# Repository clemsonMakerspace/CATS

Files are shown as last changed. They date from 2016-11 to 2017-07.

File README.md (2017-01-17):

CATS
====

The Clemson (Machinery) Access Tracking System, or CATS, is a [Creative Inquiry](http://www.clemson.edu/academics/programs/creative-inquiry/) project at Clemson University.

The goal of the project is to come up with an open-source system that can track and control machine access
at the Makerspaces on the campus.  As we work on the design process, we document our progress in our blog,
which you can find [here](http://ci.clemson.edu/blogs/cats/).

----

### Dependencies

This is a Python 3.x program dependent on the following libraries:
   1. `sys` - Python sys Libary
   2. `time` - Python time library
   3. `pymysql` - Python MySQL client
   4. `datetime` - Python datetime library
   5. `os` - Python os library (Python operating system interface)
   6. `RPi.GPIO` - package for controlling Rasberry Pi GPIO
   7. `string` - Python string library
   8. `InputDevice from evdev` - function from evdev package for Linux inputs
   9. `select from select` - Python select function from select library
   
These dependencies can be installed with the 'setup.sh' shell script found within.

### Configuration

TODO

### Usage

TODO

### License

The Clemson (Machinery) Access Tracking System is free software: you can 
redistribute it and/or modify it under the terms of the GNU Lesser General 
Public License as published by the Free Software Foundation, either version 
3 of the License, or (at your option) any later version.

The Clemson (Machinery) Access Tracking System is distributed in the hope 
that it will be useful, but WITHOUT ANY WARRANTY; without even the implied 
warranty of MERCHANTABILITY or FITNESS FOR A PARTICULAR PURPOSE.  See the
GNU Lesser General Public License for more details.

You should have received a copy of the GNU Lesser General Public License
along with this program.  If not, see <http://www.gnu.org/licenses/>

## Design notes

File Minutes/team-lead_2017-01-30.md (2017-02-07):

Team Lead Meeting Minutes
====

2017-01-30

10:10 AM - Start

####Attendees:
* Giandre Acosta
* Brice Grooms
* Owen Phillips
		
###New Meeting Formats
* Meeting minutes will be kept at all future team meetings held by Giandre, Brice, and/or Owen
* Meeting agendas will be distributed for all future team meetings held by Giandre, Brice, and/or Owen

###Team Meeting Summaries
#####Hardware
* Housing is currently discussing options
* PCB will hopefully be ready to order Friday
	* Owen will check with A. Hoover regarding purchasing requirements
	* Design will feature parallel routes for SMD and TH components
	* Will feature headers instead of raw wiring
* HID Omnikey 5321 has been recommended, will be ordered by Owen
	* Brice will submit a link for the 5321
	* Hardware team has promised to take ownership of software change for 5321

#####Software
* Software is working to introduce new devs to code base
* Brad is making headway on web admin panel - should be ready for additional help by Wednesday
		
###Goals for This Week
#####Software
* Giandre and Owen will work to setup test env with mocks for libraries like RPi.GPIO
* Team members will take ownership of certain functions and write tests
* Refactor at a later date
* Eduroam will be tested on a Raspberry Pi this week

#####Hardware
* Hardware will create BOM prior to purchasing PCBs
* Waterproofing has been de-prioritized in order to focus on immediate needs

#####Misc
* Hardware and Software leaders will debate use of Neopixel vs Traditional LEDs and select one by Friday

###Management Discussion
* Teams will utilize Waffle to track action items
* Teams should have retrospectives / standups to discuss work completed throughout the week
* Meetings should serve a purpose, anyone not necessary for the discussion should be dismissed

11:00 AM - Adjourn

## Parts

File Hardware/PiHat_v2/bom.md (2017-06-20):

Name            | Supplier | Part Number       | Quantity | Unit Cost | Link
----------------|----------|-------------------|----------|-----------|----------------------------------------------------------------------------------------------------------------
Neopixel        | Adafruit | 1655              | 5        | $0.45     | [Link](https://www.adafruit.com/product/1655)
Standoffs       | Adafruit | 2336              | 1        | $0.75     | [Link](https://www.adafruit.com/product/2336)
RPi GPIO Header | Adafruit | 2222              | 1        | $1.50     | [Link](https://www.adafruit.com/product/2222)
ATMEGA328P      | Digikey  | ATMEGA328P-AU-ND  | 1        | $2.07     | [Link](https://www.digikey.com/product-detail/en/microchip-technology/ATMEGA328P-AU/ATMEGA328P-AU-ND/1832260)
EEPROM          | Digikey  | CAT24C32WI-GOS-ND | 1        | $0.26     | [Link](https://www.digikey.com/products/en?mpart=CAT24C32WI-G&v=488)
Temp Sensor     | Digikey  | 568-4688-1-ND     | 1        | $0.74     | [Link](https://www.digikey.com/product-detail/en/nxp-usa-inc/LM75BD,118/568-4688-1-ND/1993025)
Piezo           | Digikey  | 102-1266-1-ND     | 1        | $2.08     | [Link](https://www.digikey.com/product-detail/en/cui-inc/CT-1205H-SMT-TR/102-1266-1-ND/610974)
Ethernet Jack   | Digikey  | RJHSE-5080-ND     | 1        | $0.91     | [Link](https://www.digikey.com/product-detail/en/amphenol-commercial-products/RJHSE-5080/RJHSE-5080-ND/1242687)
ISP Header      | Digikey  | 952-2120-ND       | 1        | $0.27     | [Link](https://www.digikey.com/product-detail/en/harwin-inc/M20-9980345/952-2120-ND/3728084)
1x2 Header      | Digikey  | 952-2261-ND       | 6        | $0.15     | [Link](https://www.digikey.com/product-detail/en/harwin-inc/M20-9990245/952-2261-ND/3728225)
Shunt Jumper    | Digikey  | 3M9580-ND         | 1        | $0.10     | [Link](http://www.digikey.com/scripts/DkSearch/dksus.dll?Detail&itemSeq=231061205&uq=636334990418973231)
16MHz Crystal   | Digikey  | 535-10226-1-ND    | 1        | $0.25     | [Link](https://www.digikey.com/products/en?keywords=535-10226-1-ND)
20pF Cap        | Digikey  | 311-1424-1-ND     | 2        | $0.10     | [Link](https://www.digikey.com/product-detail/en/yageo/CC0603JRNPO9BN200/311-1424-1-ND/2833730)
0.1uF Cap       | Digikey  | 311-1361-1-ND     | 1        | $0.10     | [Link](https://www.digikey.com/product-detail/en/yageo/CC0805ZRY5V9BB104/311-1361-1-ND/2103145)
1000uF Cap      | Digikey  | 493-2160-1-ND     | 1        | $0.48     | [Link](https://www.digikey.com/product-detail/en/nichicon/UWT0J102MNL1GS/493-2160-1-ND/590135)
1K Resistors    | Digikey  | 311-1.0KARCT-ND   | 4        | $0.10     | [Link](https://www.digikey.com/product-detail/en/yageo/RC0805JR-071KL/311-1.0KARCT-ND/731165)
3.9K Resistor   | Digikey  | 311-3.9KARCT-ND   | 2        | $0.10     | [Link](https://www.digikey.com/product-detail/en/yageo/RC0805JR-073K9L/311-3.9KARCT-ND/731252)
10K Resistor    | Digikey  | 311-10KARCT-ND    | 1        | $0.10     | [Link](https://www.digikey.com/product-detail/en/yageo/RC0805JR-0710KL/311-10KARCT-ND/731188)

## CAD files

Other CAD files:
Hardware/CATS Enclosure/V0.2 Drawing.SLDDRW

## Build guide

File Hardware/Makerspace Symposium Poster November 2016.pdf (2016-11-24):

RESEARCH POSTER PRESENTATION DESIGN © 2015
www.PosterPresentations.com

Makerspace equipment often has inherent risks to its users. These risks can be reduced by training operators. An additional approach to reduce these risks is to install technology that restricts access to untrained users.

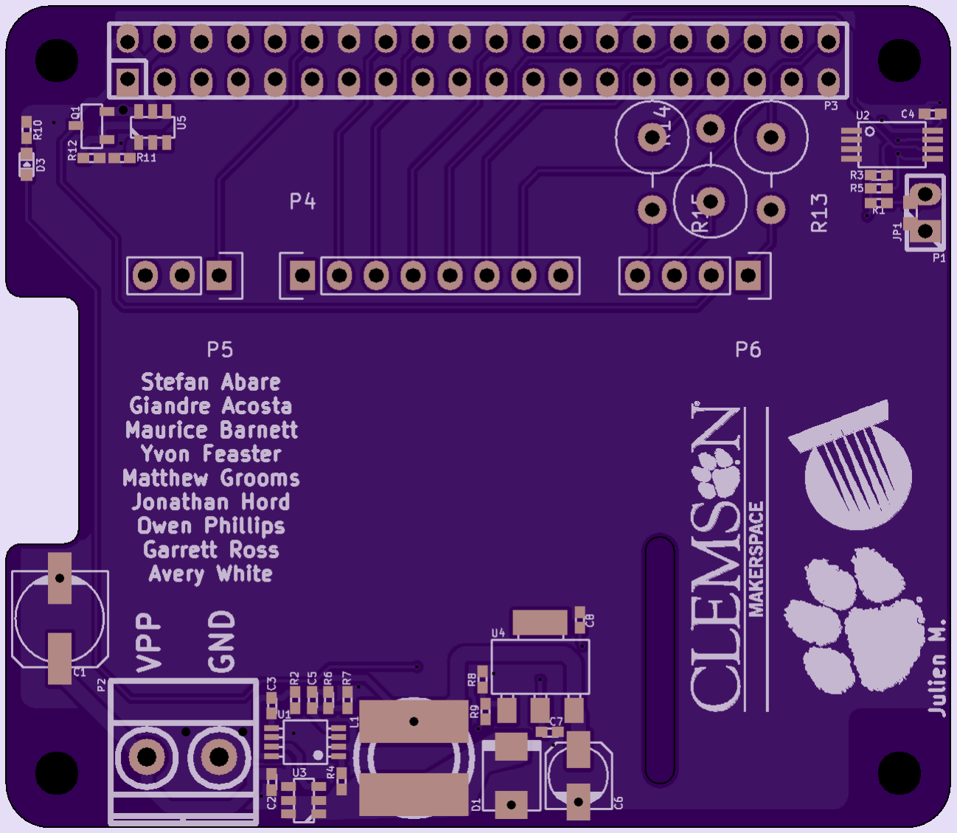
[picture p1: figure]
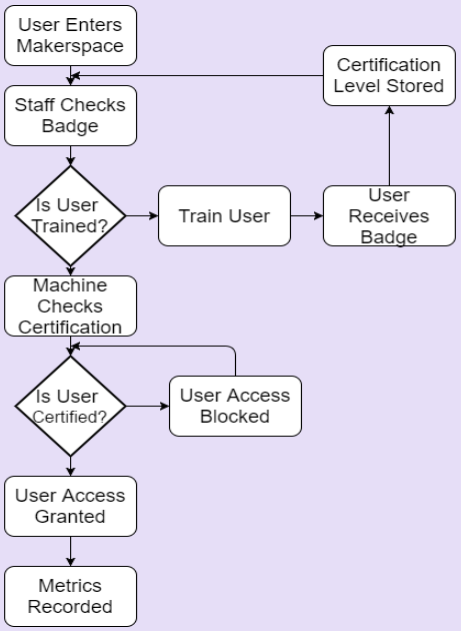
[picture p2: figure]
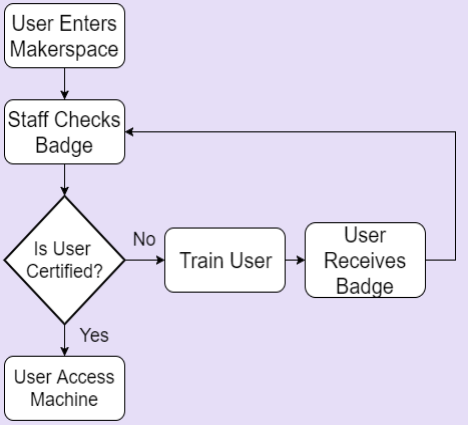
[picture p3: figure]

The Clemson [Machinery] Access Tracking System (CATS) is in development to create a more efficient way to operate a student space by automating the authentication process for a machine, so it will only power on for persons with permissions. Using CATS, facilities will be able to secure their machines by requiring students to provide credentials using their campus ID cards, and RFID card readers on machines/spaces. For double authentication a PIN number will also be required.

### I. Introduction

### II. Background

### V. Results

### IV. Methodology

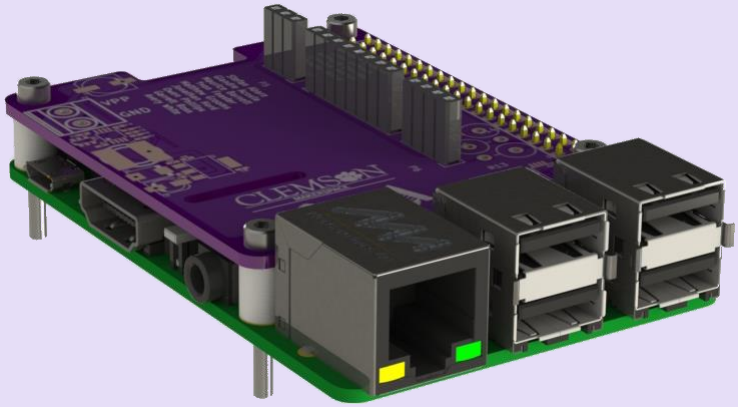
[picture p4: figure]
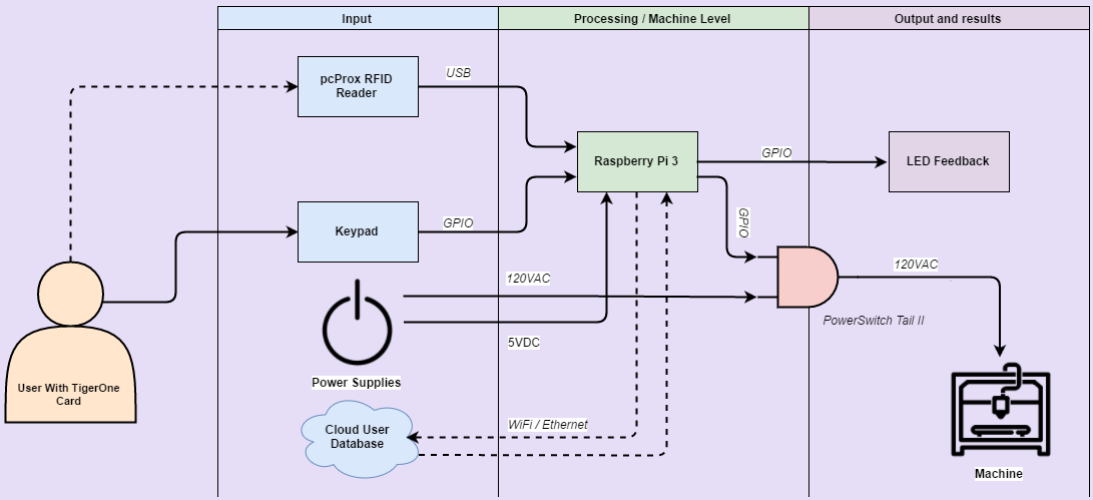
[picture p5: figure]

### VI. Conclusions

Access Protocols for Makerspaces have inherent challenges which threaten safety. The team has developed an open source technology, the CATS system, that has the ability to automate the authentication process for machines.

ophilli@g.clemson.edu¹ , jhord@g.clemson.edu

2
, sabare@g.clemson.edu

3
, gacosta@g.clemson.edu

4
, mbgroom@g.clemson.edu

5
, avery5@g.clemson.edu

6
,
mauricb@g.clemson.edu⁷
, gmross@g.clemson.edu

8
, yfeaste@g.clemson.edu

9
, todds@clemson.edu

10
, Clemson University, Clemson, SC

Owen Phillips¹
, Jonathan B. Hord

2
, Stefan Abare

3
, Giandre Acosta

4
, Matthew B. Grooms

5
, Avery White

6
, Maurice
Barnett

7
, Garrett Ross

8
, Yvon Feaster

9
, and Todd Schweisinger

10

# Development of Low Cost, Open-Source, Machinery Access Control & Tracking System by Undergraduate Team

The Creative Inquiry (CI) Program at Clemson University funds Undergraduate Research Projects. A CI team was formed in August 2016 from majors in Computer Science and Engineering, Mechanical Engineering, and Industrial Engineering to address this machine authentication challenge.

Most access protocols require a staff member to verify training credentials for each person wishing to use makerspace machines, but

Figure 5: PCB Design
of CATS Prototype

Figure 6: CATS Pi
shield with Raspberry
Pi 3

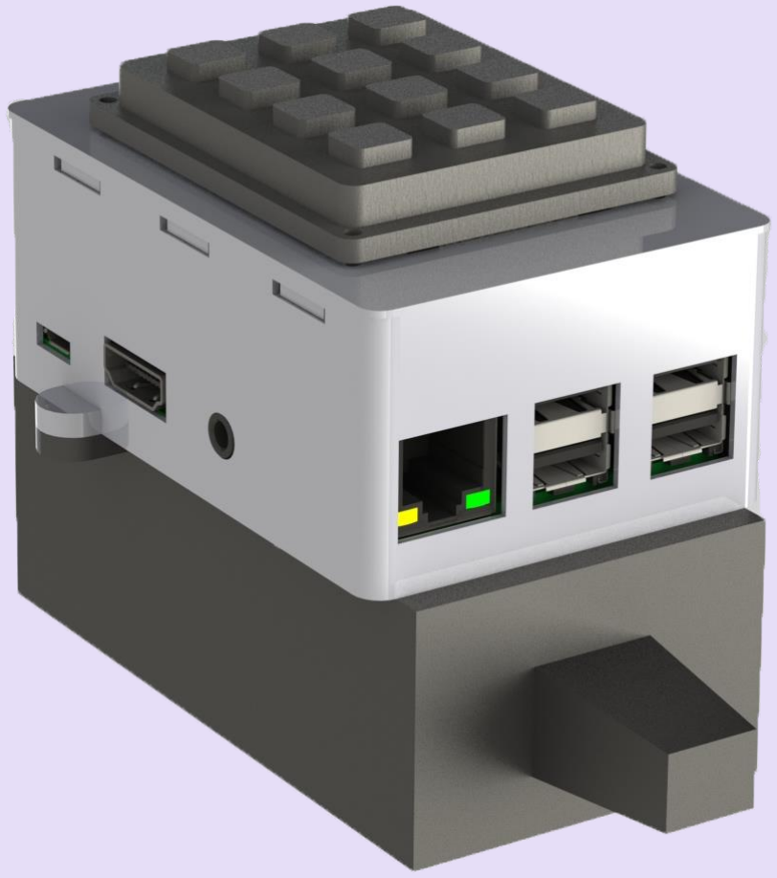
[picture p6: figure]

Figure 4: CATS Hardware Prototype

Figure 3: CATS Context Level Schematic

### III. Objective

[1] George Carlson, Kolja Windeler, “An Introduction to the MACS - Makerspace Access Control System,” MakerBarn. 2015. youtube.com/watch?v=CI3xxsBM9SE
[2] Crumpacker, Chris. "Using 3x4 Matrix Keypad with the Raspberry Pi." Crump
Projects:. N.p., 13 May | 2013. Web. 16 Sept. 2016.
[3]"How Can I Read Input from the Hosts Keyboard When Connected via SSH?" Linux. N.p., 1 Nov. 2013. Web. 28 Sept. 2016.
[4] PyMySQL Methane. "PyMySQL/PyMySQL." GitHub. N.p., Nov. 2013. Web. 20 Oct. 2016.
[5] Tutorialspoint.com. "Python 3 MySQL Database Access." Www.tutorialspoint.com. TutorialsPoint, n.d. Web. 20 Oct. 2016.

github - github.com/clemsonMakerspace/CATS
blog - ci.clemson.edu/blogs/cats/

Challenges of current access protocols can include:
●An Overloaded Staff Member
●Overly confident “I Know What I’m Doing” Users
●Accidental Machine Starts After Outage ●Effort Required to Record and Report Usage Data

Existing Solutions to Challenges Include-Makerspace Access Control System[1] - But it is not open source, which limits its application in customized student spaces.

Create an automated system, CATS, to provide an additional layer of safety by automatically restricting the power to machines and provide usage data for analysis by administrators.

The detailed logic for the CATS system can be seen in Figure 3. In contrast to Figure 1 this process will solve all the challenges from the previous access protocols and provide technical solutions to the proposed system in Figure 2.

This prototype (Figure 4) provided a proof of concept. It uses both RFID User ID and PIN authentications. This prototype was redesigned into a Pi shield to organize input and output connections.

The CATS Pi shield (Figure 5) organizes inputs (keypad) and outputs (Status LED, Power to Machine).

Figure 1: Human
Dependent Credential
Checks

Figure 2: Electronic
Control of Access

To solve the challenges of a human dependent system (Figure 1) a new system must be designed that supplements the process with electronic back checks (Figure 2).

This work was supported in part by the Clemson University Creative Inquiry Program
The presentation of this work was supported in part by - ISAM

The CATS Pi shield connects to a Raspberry Pi 3 (Figure 6). The Pi 3 redirects inputs given through the RFID reader and keypad to a MySQL Database.

### VII. References

### V. Results

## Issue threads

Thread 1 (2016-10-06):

matrix_keypad Installation Permission Errors

ophilli, 2016-10-06:
Running Raspbian Jessie Lite 2016-09-23, and the setup script is not happy with user permissions for installing matrix_keypad.

./setup.sh > setup_log.txt
```
Hit http://archive.raspberrypi.org jessie InRelease
Hit http://mirrordirector.raspbian.org jessie InRelease
Hit http://archive.raspberrypi.org jessie/main armhf Packages
Hit http://mirrordirector.raspbian.org jessie/main armhf Packages
Hit http://archive.raspberrypi.org jessie/ui armhf Packages
Hit http://mirrordirector.raspbian.org jessie/contrib armhf Packages
Hit http://mirrordirector.raspbian.org jessie/non-free armhf Packages
Hit http://mirrordirector.raspbian.org jessie/rpi armhf Packages
Ign http://archive.raspberrypi.org jessie/main Translation-en_GB
Ign http://archive.raspberrypi.org jessie/main Translation-en
Ign http://archive.raspberrypi.org jessie/ui Translation-en_GB
Ign http://archive.raspberrypi.org jessie/ui Translation-en
Ign http://mirrordirector.raspbian.org jessie/contrib Translation-en_GB
Ign http://mirrordirector.raspbian.org jessie/contrib Translation-en
Ign http://mirrordirector.raspbian.org jessie/main Translation-en_GB
Ign http://mirrordirector.raspbian.org jessie/main Translation-en
Ign http://mirrordirector.raspbian.org jessie/non-free Translation-en_GB
Ign http://mirrordirector.raspbian.org jessie/non-free Translation-en
Ign http://mirrordirector.raspbian.org jessie/rpi Translation-en_GB
Ign http://mirrordirector.raspbian.org jessie/rpi Translation-en
Reading package lists...
Reading package lists...
Building dependency tree...
Reading state information...
The following extra packages will be installed:
  python-pkg-resources
Suggested packages:
  python-distribute python-distribute-doc
The following NEW packages will be installed:
  python-pkg-resources python-setuptools
0 upgraded, 2 newly installed, 0 to remove and 13 not upgraded.
Need to get 306 kB of archives.
After this operation, 957 kB of additional disk space will be used.
Do you want to continue? [Y/n] Get:1 http://mirrordirector.raspbian.org/raspbian/ jessie/main python-pkg-resources all 5.5.1-1 [64.4 kB]
Get:2 http://mirrordirector.raspbian.org/raspbian/ jessie/main python-setuptools all 5.5.1-1 [242 kB]
Fetched 306 kB in 0s (362 kB/s)
Selecting previously unselected package python-pkg-resources.
(Reading database ...
(Reading database ... 5%
(Reading database ... 10%
(Reading database ... 15%
(Reading database ... 20%
(Reading database ... 25%
(Reading database ... 30%
(Reading database ... 35%
(Reading database ... 40%
(Reading database ... 45%
(Reading database ... 50%
(Reading database ... 55%
(Reading database ... 60%
(Reading database ... 65%
(Reading database ... 70%
(Reading database ... 75%
(Reading database ... 80%
(Reading database ... 85%
(Reading database ... 90%
(Reading database ... 95%
(Reading database ... 100%
(Reading database ... 31216 files and directories currently installed.)
Preparing to unpack .../python-pkg-resources_5.5.1-1_all.deb ...
Unpacking python-pkg-resources (5.5.1-1) ...
Selecting previously unselected package python-setuptools.
Preparing to unpack .../python-setuptools_5.5.1-1_all.deb ...
Unpacking python-setuptools (5.5.1-1) ...
Setting up python-pkg-resources (5.5.1-1) ...
Setting up python-setuptools (5.5.1-1) ...
Reading package lists...
Building dependency tree...
Reading state information...
Reading package lists...
Building dependency tree...
Reading state information...
The following extra packages will be installed:
  python-chardet python-colorama python-distlib python-html5lib
  python-ndg-httpsclient python-openssl python-pyasn1 python-requests
  python-six python-urllib3 python-wheel
Suggested packages:
  python-genshi python-lxml python-openssl-doc python-openssl-dbg doc-base
Recommended packages:
  python-dev-all
The following NEW packages will be installed:
  python-chardet python-colorama python-distlib python-html5lib
  python-ndg-httpsclient python-openssl python-pip python-pyasn1
  python-requests python-six python-urllib3 python-wheel
0 upgraded, 12 newly installed, 0 to remove and 13 not upgraded.
Need to get 903 kB of archives.
After this operation, 4,084 kB of additional disk space will be used.
Do you want to continue? [Y/n] Get:1 http://mirrordirector.raspbian.org/raspbian/ jessie/main python-chardet all 2.3.0-1 [96.2 kB]
Get:2 http://mirrordirector.raspbian.org/raspbian/ jessie/main python-colorama all 0.3.2-1 [20.3 kB]
Get:3 http://mirrordirector.raspbian.org/raspbian/ jessie/main python-distlib all 0.1.9-1 [113 kB]
Get:4 http://mirrordirector.raspbian.org/raspbian/ jessie/main python-six all 1.8.0-1 [12.6 kB]
Get:5 http://mirrordirector.raspbian.org/raspbian/ jessie/main python-html5lib all 0.999-3 [84.0 kB]
Get:6 http://mirrordirector.raspbian.org/raspbian/ jessie/main python-openssl armhf 0.13.1-2 [85.5 kB]
Get:7 http://mirrordirector.raspbian.org/raspbian/ jessie/main python-ndg-httpsclient all 0.3.2-1 [20.5 kB]
Get:8 http://mirrordirector.raspbian.org/raspbian/ jessie/main python-urllib3 all 1.9.1-3 [55.4 kB]
Get:9 http://mirrordirector.raspbian.org/raspbian/ jessie/main python-pip all 1.5.6-5 [114 kB]
Get:10 http://mirrordirector.raspbian.org/raspbian/ jessie/main python-requests all 2.4.3-6 [204 kB]
Get:11 http://mirrordirector.raspbian.org/raspbian/ jessie/main python-pyasn1 all 0.1.7-1 [49.3 kB]
Get:12 http://mirrordirector.raspbian.org/raspbian/ jessie/main python-wheel all 0.24.0-1 [47.5 kB]
Fetched 903 kB in 2s (361 kB/s)
Selecting previously unselected package python-chardet.
(Reading database ...
(Reading database ... 5%
(Reading database ... 10%
(Reading database ... 15%
(Reading database ... 20%
(Reading database ... 25%
(Reading database ... 30%
(Reading database ... 35%
(Reading database ... 40%
(Reading database ... 45%
(Reading database ... 50%
(Reading database ... 55%
(Reading database ... 60%
(Reading database ... 65%
(Reading database ... 70%
(Reading database ... 75%
(Reading database ... 80%
(Reading database ... 85%
(Reading database ... 90%
(Reading database ... 95%
(Reading database ... 100%
(Reading database ... 31318 files and directories currently installed.)
Preparing to unpack .../python-chardet_2.3.0-1_all.deb ...
Unpacking python-chardet (2.3.0-1) ...
Selecting previously unselected package python-colorama.
Preparing to unpack .../python-colorama_0.3.2-1_all.deb ...
Unpacking python-colorama (0.3.2-1) ...
Selecting previously unselected package python-distlib.
Preparing to unpack .../python-distlib_0.1.9-1_all.deb ...
Unpacking python-distlib (0.1.9-1) ...
Selecting previously unselected package python-six.
Preparing to unpack .../python-six_1.8.0-1_all.deb ...
Unpacking python-six (1.8.0-1) ...
Selecting previously unselected package python-html5lib.
Preparing to unpack .../python-html5lib_0.999-3_all.deb ...
Unpacking python-html5lib (0.999-3) ...
Selecting previously unselected package python-openssl.
Preparing to unpack .../python-openssl_0.13.1-2_armhf.deb ...
Unpacking python-openssl (0.13.1-2) ...
Selecting previously unselected package python-ndg-httpsclient.
Preparing to unpack .../python-ndg-httpsclient_0.3.2-1_all.deb ...
Unpacking python-ndg-httpsclient (0.3.2-1) ...
Selecting previously unselected package python-urllib3.
Preparing to unpack .../python-urllib3_1.9.1-3_all.deb ...
Unpacking python-urllib3 (1.9.1-3) ...
Selecting previously unselected package python-requests.
Preparing to unpack .../python-requests_2.4.3-6_all.deb ...
Unpacking python-requests (2.4.3-6) ...
Selecting previously unselected package python-pip.
Preparing to unpack .../python-pip_1.5.6-5_all.deb ...
Unpacking python-pip (1.5.6-5) ...
Selecting previously unselected package python-pyasn1.
Preparing to unpack .../python-pyasn1_0.1.7-1_all.deb ...
Unpacking python-pyasn1 (0.1.7-1) ...
Selecting previously unselected package python-wheel.
Preparing to unpack .../python-wheel_0.24.0-1_all.deb ...
Unpacking python-wheel (0.24.0-1) ...
Processing triggers for man-db (2.7.0.2-5) ...
Setting up python-chardet (2.3.0-1) ...
Setting up python-colorama (0.3.2-1) ...
Setting up python-distlib (0.1.9-1) ...
Setting up python-six (1.8.0-1) ...
Setting up python-html5lib (0.999-3) ...
Setting up python-openssl (0.13.1-2) ...
Setting up python-ndg-httpsclient (0.3.2-1) ...
Setting up python-urllib3 (1.9.1-3) ...
Setting up python-requests (2.4.3-6) ...
Setting up python-pip (1.5.6-5) ...
Setting up python-pyasn1 (0.1.7-1) ...
Setting up python-wheel (0.24.0-1) ...
Processing triggers for python-support (1.0.15) ...
Reading package lists...
Building dependency tree...
Reading state information...
The following extra packages will be installed:
  dh-python libmpdec2 libpython3-stdlib libpython3.4-minimal
  libpython3.4-stdlib python3-minimal python3.4 python3.4-minimal
Suggested packages:
  python3-doc python3-tk python3-venv python3.4-venv python3.4-doc
  binfmt-support
The following NEW packages will be installed:
  dh-python libmpdec2 libpython3-stdlib libpython3.4-minimal
  libpython3.4-stdlib python3 python3-minimal python3.4 python3.4-minimal
0 upgraded, 9 newly installed, 0 to remove and 13 not upgraded.
Need to get 4,259 kB of archives.
After this operation, 17.2 MB of additional disk space will be used.
Do you want to continue? [Y/n] Get:1 http://mirrordirector.raspbian.org/raspbian/ jessie/main libmpdec2 armhf 2.4.1-1 [65.8 kB]
Get:2 http://mirrordirector.raspbian.org/raspbian/ jessie/main libpython3.4-minimal armhf 3.4.2-1 [483 kB]
Get:3 http://mirrordirector.raspbian.org/raspbian/ jessie/main libpython3.4-stdlib armhf 3.4.2-1 [2,011 kB]
Get:4 http://mirrordirector.raspbian.org/raspbian/ jessie/main python3.4 armhf 3.4.2-1 [204 kB]
Get:5 http://mirrordirector.raspbian.org/raspbian/ jessie/main python3.4-minimal armhf 3.4.2-1 [1,355 kB]
Get:6 http://mirrordirector.raspbian.org/raspbian/ jessie/main libpython3-stdlib armhf 3.4.2-2 [18.1 kB]
Get:7 http://mirrordirector.raspbian.org/raspbian/ jessie/main python3 armhf 3.4.2-2 [21.2 kB]
Get:8 http://mirrordirector.raspbian.org/raspbian/ jessie/main python3-minimal armhf 3.4.2-2 [34.7 kB]
Get:9 http://mirrordirector.raspbian.org/raspbian/ jessie/main dh-python all 1.20141111-2 [66.4 kB]
Fetched 4,259 kB in 1s (2,264 kB/s)
Selecting previously unselected package libmpdec2:armhf.
(Reading database ...
(Reading database ... 5%
(Reading database ... 10%
(Reading database ... 15%
(Reading database ... 20%
(Reading database ... 25%
(Reading database ... 30%
(Reading database ... 35%
(Reading database ... 40%
(Reading database ... 45%
(Reading database ... 50%
(Reading database ... 55%
(Reading database ... 60%
(Reading database ... 65%
(Reading database ... 70%
(Reading database ... 75%
(Reading database ... 80%
(Reading database ... 85%
(Reading database ... 90%
(Reading database ... 95%
(Reading database ... 100%
(Reading database ... 31855 files and directories currently installed.)
Preparing to unpack .../libmpdec2_2.4.1-1_armhf.deb ...
Unpacking libmpdec2:armhf (2.4.1-1) ...
Selecting previously unselected package libpython3.4-minimal:armhf.
Preparing to unpack .../libpython3.4-minimal_3.4.2-1_armhf.deb ...
Unpacking libpython3.4-minimal:armhf (3.4.2-1) ...
Selecting previously unselected package libpython3.4-stdlib:armhf.
Preparing to unpack .../libpython3.4-stdlib_3.4.2-1_armhf.deb ...
Unpacking libpython3.4-stdlib:armhf (3.4.2-1) ...
Selecting previously unselected package python3.4-minimal.
Preparing to unpack .../python3.4-minimal_3.4.2-1_armhf.deb ...
Unpacking python3.4-minimal (3.4.2-1) ...
Selecting previously unselected package python3.4.
Preparing to unpack .../python3.4_3.4.2-1_armhf.deb ...
Unpacking python3.4 (3.4.2-1) ...
Selecting previously unselected package python3-minimal.
Preparing to unpack .../python3-minimal_3.4.2-2_armhf.deb ...
Unpacking python3-minimal (3.4.2-2) ...
Selecting previously unselected package libpython3-stdlib:armhf.
Preparing to unpack .../libpython3-stdlib_3.4.2-2_armhf.deb ...
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

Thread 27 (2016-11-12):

When switching cards quickly

r3cebarnett, 2016-11-12:
It doesn't deny access for some reason. Someone could bypass this by putting in a good card and pin and quickly switching to another card, it doesn't cut access.

ophilli, 2016-11-12:
Fixed in commit 4af7ff2.

Closed 2016-11-12.

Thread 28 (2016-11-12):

Invalid PIN does not re-prompt

r3cebarnett, 2016-11-12:
You have to take off the card and put it back on.

ophilli, 2016-11-12:
Fixed in commit 4af7ff2.

ophilli, 2016-11-12:
@mbgroom I am still able to reproduce this bug.

gacosta1, 2017-01-11:
Invalid PIN does re-prompt now, but I have to set a timer for maybe like 3 seconds for after it re-prompts because once the user is asked to re enter their PIN, it will sit on that option until they type a 4 digit PIN whether it's correct or not. hope that makes sense..

gacosta1, 2017-01-11:
Only option to solve that would be to use threading. If anyone else has ideas let me know. Cause as of now threading would allow us to listen for the user input while having a timer in the background.

gacosta1, 2017-01-11:
@gacosta1 Also threading would have to listen to the card reader as well as waiting for keypad input

ophilli, 2017-01-11:
@gacosta1 Sounds like we need to diagram the authentication flow.

gacosta1, 2017-01-12:
Most likely my friend.

ophilli, 2017-01-12:
@gacosta1 @gmross Can you put together an auth flow chart?

gacosta1, 2017-01-12:
As I sit in my Intro to Operating System class, I thought of a way that I could fix this little problem we have here. He's been talking about interrupts. Interrupts can be used to prevent issues or misuse in the operating system or memory or files. Sooo I think I can use an interrupt to set a time in the background while the user is trying to enter their PIN. Even if the card has been taken off of the card reader, the system will count for a certain time and if the user hasn't entered something it will lock them out.

gacosta1, 2017-01-12:
I'll try to code it when I get home.

r3cebarnett, 2017-01-14:
Just made a pretty dope auth flow chart. Will commit in a few.

gacosta1, 2017-01-15:
It is finished. Rejoice.

r3cebarnett, 2017-01-15:
gj g i'm proud

gacosta1, 2017-01-15:
Found a bug while testing, but I fixed it. Official finished. PR coming soon.

ophilli, 2017-01-15:
Can you write unit tests for this PR?

Owen Phillips

On Jan 15, 2017 2:36 AM, "Giandre Acosta" <notifications@github.com> wrote:

Found a bug while testing, but I fixed it. Official finished. PR coming
soon.

—
You are receiving this because you modified the open/close state.
Reply to this email directly, view it on GitHub
<https://github.com/clemsonMakerspace/CATS/issues/28#issuecomment-272679295>,
or mute the thread
<https://github.com/notifications/unsubscribe-auth/AA65BqQvv4oYXjjGh4VaGzqM9QgMla4Lks5rScxrgaJpZM4KwUSe>
.

gacosta1, 2017-01-19:
Will post PR tomorrow morning at 10AM sharp.

ophilli, 2017-01-19:
Lol wat

Owen Phillips

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

gacosta1, 2017-01-19:
Will create a PR tomorrow morning at 10AM sharp.

Closed 2017-01-22.

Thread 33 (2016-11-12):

LED Anode should be connected to 3.3v, not 5v.

r3cebarnett, 2016-11-12:

ophilli, 2016-11-12:
GPIO on the Raspberry Pi provides 3.3v as a logic high. Currently the LED anode is being supplied with 5v, leaving 1.7v across the resistor and the LED.

The LED anode should be connected to the 3.3v rail on the Pi.

Closed 2017-02-01.

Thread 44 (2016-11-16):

Led flash after every key stroke

gacosta1, 2016-11-16:
We want the LED to blink every time a user types on the keypad. Maybe the color blue? or purple? We can further discuss this in the team meeting.

gacosta1, 2016-12-10:
Completed

ophilli, 2016-12-10:
Re-opened pending pull request with code changes that resolve this issue.

ophilli, 2016-12-11:
Enhancement implemented in #53

Closed 2016-12-11.

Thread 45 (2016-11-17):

Create Error logs in SQL Server

gacosta1, 2016-11-17:
create a new database that contains error logs with:
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
**We can settle this as a team in the next team meeting**

gacosta1, 2016-11-18:
Then at the end of the day at 12:00 AM or an automated file will be created with users who tried to use the machine but did not have permission/untrained or machine errors were found or etc....
Food for thought.

ophilli, 2016-11-18:
We could call Twillio or Sendgrid to automatically notify admins when
authorization fails.

Owen Phillips
Clemson University Class of 2019
B.S. Computer Engineering
Student Director | Clemson University Makerspace
Board of Directors | Clemson University 3D Printing Organization
C: 864.633.0499

On Thu, Nov 17, 2016 at 9:18 PM, Giandre Acosta <notifications@github.com>
wrote:

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

gacosta1, 2016-11-18:
Yes!! I like that!

r3cebarnett, 2016-11-18:
Pretty good idea. I'll quickly make a database for it right now because why
not.

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

ophilli, 2016-11-18:
I think this belongs in the Events table. That's what they are - no reason to call a new table for them.

gacosta1, 2016-11-18:
Sweeet thanks Maurice! I created one, but just append to the Events db

ophilli, 2016-11-18:
MySQL is a relational database - it's good design to avoid duplicating unnecessary data.

We've already got a table of CUIDs, and MachineIDs. Those contain all the first name, last name, machine type info we need.

I would like to propose the following:

CUID* | MachineID* | Timestamp* | Status
-------|--------------|---------------|---
C12345678 | 001 |  1970-01-01 00:00:01 | 1
C23456789 | 010 |  1970-01-01 00:00:01 | 2
C34567890 | 100 |  1970-01-01 00:00:01 | 3
>\* Denotes Primary Key

gacosta1, 2016-11-18:
Seems clean and straight to the point. I like it. Maurice can you handle that? If not, let me know.

gacosta1, 2016-12-10:
Error Log for database complete. We just need to figure out what we're going to use to notify the Admin.

ophilli, 2016-12-10:
Re-opened pending pull request with code changes that resolve this issue.

ophilli, 2016-12-11:
Enhancement implemented in #53

Closed 2016-12-11.

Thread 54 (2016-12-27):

Unit Testing

gacosta1, 2016-12-27:
Test code for functionality and correctness

ophilli, 2017-01-07:
Any ideas on how we can break this up into more actionable items?

gacosta1, 2017-01-11:
Elaborate on that please.

ophilli, 2017-01-11:
I guess I need a "How to Unit Test for Dummies". Do we need a testing framework?

r3cebarnett, 2017-02-01:
Will be working on it this week

r3cebarnett, 2017-02-02:
Started writing nose tests. Check my progress in nose branch.

Closed 2017-02-07.

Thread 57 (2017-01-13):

Resolder Relay Header on Clear Cased Board

ophilli, 2017-01-13:
The CATS Shield in the clear case needs to have the relay header re-soldered.

ophilli, 2017-05-13:
Closing due to plans to replace all old HATS.

Closed 2017-05-13.

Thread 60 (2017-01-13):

Local Hostname Resolution Fails

ophilli, 2017-01-13:
Attempts to resolve local hostnames such as octopi.local, CATS-SQL.local, or series1-10306.local all fail on a standard LAN. These function normally on the octopi distro, and my Win7 machine.

This can be temporarily resolved by configuring a static map in our router for the desired MAC/IP combos.

ophilli, 2017-01-13:
A static map of CATS-SQL wasn't enough to resolve the issue between CATS-Beta-2 and CATS-SQL - despite resolving the issue for CATS-Beta-2 and the TAM printers. The static map and an installation of [Netatalk](https://en.wikipedia.org/wiki/Netatalk) was enough to allow communication.

However, a cold boot of CATS-Beta-2 still fails as seen in the [Boot logs].(https://gist.github.com/ophilli/ab2b7e8924690d181a47d056f93f2ffa)

ophilli, 2017-01-13:
It appears that Netatalk works intermittently. Not sure what is going on.

ophilli, 2017-01-20:
Today on two of my Octopi computers I was unable to ping any of the other Raspberry Pis.

I removed all of the static dhcp allocations and rebooted everything - this appears to have resolved the issue.

ophilli, 2017-01-25:
I'm wondering if this is a problem with the LAN in the Makerspace now. We're having a lot of weird even with some Octopi machines.

ophilli, 2017-01-27:
Recently I swapped everything over to the switch in the Makerspace, rather than through the router. This has allowed me to ping all the other .local domains. There was one older Raspberry Pi that I wasn't able to ping, and installing avahi-daemon on that machine promptly resolved that.

Will continue to monitor for further updates.

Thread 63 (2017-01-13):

CATS HAT v2

ophilli, 2017-01-13:
Currently our CATS shield is just that - a shield. The next step will be to convert it to a [HAT](https://www.raspberrypi.org/blog/introducing-raspberry-pi-hats/). This means that a connected Pi would be able to identify our CATS HAT and automatically configure the GPIOs and drivers we need for the board.

Please see the [tech specs](https://github.com/raspberrypi/hats).

- [x] #48 Commit CATS Alpha Hardware Designs
- [ ] #57 Solder Repair
- [x] #33 LED Anode 3v
- [ ] #64 ID EEPROM Programming

mbgroom, 2017-01-29:
The new PCB will be designed by 2/03/17 if time permits. Only a few changes need to be made. We will need to order a few different headers for the new PCB design. While we wait on the PCBs to come in we will order the new:
*headers
*LEDs
*resistors
*clips

Closed 2017-02-01.

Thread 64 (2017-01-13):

Program CATS HAT EEPROM

ophilli, 2017-01-13:
The CATS HAT requires an ID EEPROM that identifies some fun stuff like vendor info and GPIO mappings.

Please see the following:
* [HATS General Spec](https://github.com/raspberrypi/hats)
* [ID EEPROM data format spec](https://github.com/raspberrypi/hats/blob/master/eeprom-format.md)
* [ID EEPROM sample tools and documentation](https://github.com/raspberrypi/hats/blob/master/eepromutils)

ophilli, 2017-01-19:
Quit closing things that shouldn't be closed @mbgroom

ophilli, 2017-01-23:
Bump for @mbgroom

SSStephens78, 2023-06-17:
Hello my name is Shemeka and I’m from India and I’m looking for a scholarship to help me out with a project for a small business please help me with a small amount please 🙏🏾

SSStephens78, 2023-06-17:
Also I don’t know what to say to you but I’m going through a lot right now and I’m homeless trying to find someone that can help me with my bills!! Lord knows I need help!! I don’t have any money for this but I believe in Blessings!! I’m broke!  Broke but still happy with my life. I’m still learning how to do things and how to be happy! I have no parents only my kids. I have several of ideas but don’t know how to get them into making

SSStephens78, 2023-06-17:
Please help

Mohamedrabee6, 2024-07-10:
ه

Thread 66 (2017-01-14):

Get Cheaper Scanner to Work

r3cebarnett, 2017-01-14:
HID OMNIKEY 5421. Will update with more info as I get it.

ophilli, 2017-01-14:
@r3cebarnett * [OMNIKEY User Guide](http://www.hidglobal.com/node/5231)
* [OMINKEY 5421 Datasheet](https://www.hidglobal.com/node/20413)
* [OMNIKEY Contactless Developer Guide]
(http://www.hidglobal.com/node/5487)

r3cebarnett, 2017-01-14:
Hot reads right now, if we can decompile and interpret a certain dll we can pull the info straight from there. Trying to find more info on which dll and testing with a decompiler to accurately get info.

ophilli, 2017-01-14:
Skip to Appendix A - looks like that might be the most relevant part for us.

ophilli, 2017-01-14:
Appendix A of the Contactless Developer Guide.

r3cebarnett, 2017-01-14:
I'm not even looking at the dev guide aorn, I'm setting up stuff on my laptop to test things. Notable little quirk I found, when the card is inserted all the way it seems to freeze to scan for the smart chip whereas it doesn't take any time contactless. There's some sort of switch in it.

r3cebarnett, 2017-01-14:
A.7.1 is looking like the thing to really look at. APDU is a buzz word we might want to learn about.

r3cebarnett, 2017-01-14:
Gonna stop and play a game because I'm a kid in college and want a life but, I have some stuff that I found around StackOverflow.

http://stackoverflow.com/questions/4497671/contact-less-card-through-an-omnikey-how-to-get-uid?rq=1

This above approach uses C#. From what I understand C# is Windows only, at least in this situation described in the StackOverflow post. Perhaps we could use the methods discussed in there to help us.

Notable info: The protocol is ISO 15693. Apparently this matters with how you approach it. I haven't specifically found a Python thing but there are definitely people out there that have done it in different programs. We can still get it from a dll apparently but I haven't been able to find a program that will decompile winscard.dll which is apparently our cash cow.

Notable dll's to worry about:
cxru0x64.sys
scarddlg.dll
scardsvr.dll
winscard.dll

When testing for UID and ATR (for those out of the loop, the UID is "Unique ID" and ATR is "Action-to-Reset" which is basically parameters on how the card reacts to the reader), make sure you use HID OMNIKEY Workbench because the UI is nice and easy. Drivers are on http://hidglobal.com/drivers/ .

Important: The ATR is NOT unique. They are expected to be the same if the type of the card is same. My ATR = Your ATR != USC's ATR. This can be used for preemptive authentication, kind of like we already have in main.py line 65, if we stick with this new reader.

I'm going to go ahead and assign Brice and Thor to this project because I know that they have specific interest in this. Sorry that I kinda rambled.

mbgroom, 2017-01-29:
Called HID asking for assistance and their response was rather irritating.  They told us we would need to either pay for licensing or use a licensed secure host to access the "weigand data".

 Maurice believes that if we were to use an Omnikey 5321 then the software that we previously found will work.  We have discussed this and I understand why the 5321 may work when the 5421 does not.  We are ready to order a 5321 to test with.  Until then, this issue is on hold.

r3cebarnett, 2017-01-30:
I talked to Owen about it and made a pretty good case for purchasing the 5321 and even implementing it until we get into the finalization process. He said he would like to think about it and see if it's worth it or not. He asked me to put some libraries that I found here though so he can play around.

librfid, openct, pyscard, smartcard, nfcutils, RFIDIOt are some.

mbgroom, 2017-01-30:
There is a used 5321 for sale that we can try out for a negligible cost. Here's the link:
http://www.ebay.com/itm/HID-Fargo-Omnikey-5321-USB-Smartcard-Reader-/272512464833?_trksid=p2385738.m2548.l4275

mbgroom, 2017-01-30:
And a link for a lot of 10 of them:
http://www.ebay.com/itm/Lot-of-10-HID-Omnikey-5321-Smart-Card-Reader-/222227863587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

r3cebarnett, 2017-02-07:
Waiting for funding :)

r3cebarnett, 2017-03-01:
Once #122 goes through I'll get to playing around with libraries again.

ophilli, 2017-04-07:
@r3cebarnett @mbgroom Please update.

ophilli, 2017-05-13:
Closing due to being outside scope of project.

Closed 2017-05-13.

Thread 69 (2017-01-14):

Diagnose Relay Failure

ophilli, 2017-01-14:
Yesterday I accidentally let the magic smoke out of one of the power switch tails. We'll need to investigate what happened and figure out how to prevent it from reoccurring.

r3cebarnett, 2017-01-17:
After contacting the company that makes this, I received some help.

The message I received:

"Maurice,

Appears the MOV failed. The MOV in this unit is rated at 140 vac rms and is used to protect the relay contacts against power line surges and load spikes. This has happened only once before and that was because the unit was accidentally connected to 220 volt mains. Is there any possibility that that could have happened in this case? (Unit was used in a factory that normally tested equipment to be sent overseas and someone forgot to switch the links on the step-up transformer back to 120 vac from 220 vac.)

Steve"

ophilli, 2017-01-17:
Maurice thanks for the prompt research into this issue!

* I was never informed of any 220vac outlets in the Watt 110 - therefore I think it's very unlikely that occurred.
    * I will test the outlets on that side of the room today to verify their voltages.
* The Powerswitch Tail should have been wired up as depicted [here.](https://github.com/clemsonMakerspace/CATS/blob/devel/Hardware/Alpha_Wiring%20Schematic_schem.pdf)
    * It is possible that the ```+in``` and ```-in``` pins on the relay were swapped - but that should have at most fed the relay with -3.3vdc
* Additionally we have extensively operated this relay with no load, for what that's worth.

ophilli, 2017-01-17:
@ophilli It appears that there was 208vac in the Makerspace. The Power switch tail was connected to this circuit - which seems likely to be the point of failure.

I am following up with the Facilities Manager for the Watt Family Innovation Center to address this.

ophilli, 2017-01-20:
Incident Report from January 18th, 2017
-----

Summary:

The Power Distribution Unit for our Print Pod is outputting 208vac, despite being rated for 120vac only. The outlets on this Power Distribution Unit are NELA 5-20R, which students expect to deliver 120vac. We had one student device fail catastrophically already.

The Power Distribution Unit is connected to what should be a 30A 120V circuit that was installed specifically for the Makerspace. Tim Howard has indicated that he will have an electrician brought out as soon as possible.

Extended Report:

On Friday a student connected a device (Powerswitch Tail II) to the Tripp Lite PDUMH30 power distribution unit (PDU) on the Print Pod. Upon closing the circuit this device experienced a catastrophic internal failure. No students were injured during this event, and the damaged device was immediately disconnected from power.

On Monday one of the students contacted the manufacturer of the device regarding the incident. The manufacturer stated that this type of failure has occurred only once before. In that incident the device was accidentally connected to a 220vac.

On Tuesday, the first business day since the incident I inspected the circuit with a multimeter and found that the PDU was distributing 208vac. The PDU has a recommended electrical service of 30A 120V. It features NEMA 5-20R outlets, and a NEMA L5-30P input cable. Upon discovering that the PDU was outputting 208vac I immediately spoke with Tim Pruett, who helped me verify that my readings were correct. We then disconnected the PDU from the circuit.

We have over $3,600 in 120vac only equipment connected to this PDU, alongside another $20,000 in equipment that is rated to support 100-240vac. The potential property damage was extremely large if this had not been caught sooner. The possible injuries that could have occurred to a student are even more grave, and we are very lucky to have caught this with such little damage.

I spoke with Tim Howard late Tuesday afternoon and he agreed that the readings were abnormal, and he told me he would reach out to University Facilities and have an electrician brought out as soon as possible.

-----
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

ophilli, 2017-01-20:
Following the incident report I submitted above our Research Safety contact, as well as our faculty advisor requested that we discontinue use of all electrical circuits in the Makerspace until they were cleared by an Electrician.

The electricians inspected the space on January 18th, and January 19th. We were cleared to use the other circuits on the 19th. I have also been told that an electrician will be able to correct the faulty circuit tomorrow, the 20th.

Closed 2017-01-20.

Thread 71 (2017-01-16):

Housing V2

mbgroom, 2017-01-16:
Need a more secure housing for the CATS system.

mbgroom, 2017-01-19:
Brad will help redesign the CATS housing and teach Josh how to use Solidworks.

Sabare3, 2017-03-13:
CATS Enclosure V 0.2 has been created

Closed 2017-03-13.

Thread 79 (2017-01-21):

Register on CATS Wordpress

ophilli, 2017-01-21:
You should have received an email with the instructions - please fill it out and get your account setup.

If I've assigned this to you it's because you haven't setup your account.

ophilli, 2017-01-23:
@JamacTheQuack just following up on this.

r3cebarnett, 2017-02-07:
Bump

ophilli, 2017-02-07:
I believe Josh was able to resolve his issue. @jamcmil please close this issue if that is the case.

Closed 2017-02-08.

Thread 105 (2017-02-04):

CATS Weekly Blog Post

ophilli, 2017-02-04:
http://ci.clemson.edu/blogs/cats/wp-admin/

Here are a few sample blog topics:

* Hardware Team & Software Team Current Assignments & how they lead to the final goal
* Personal Goals & Accomplishments for the Project
* Technical Analysis of an aspect of the project

Please include lots of pictures!

Due 2017-02-13

ophilli, 2017-02-13:
@mbgroom This is a reminder that your blog post is due today.

ophilli, 2017-02-14:
@mbgroom I am following up on your past-due blog post. Please complete today.

Closed 2017-02-27.

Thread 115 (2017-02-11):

Web Form to Add Machines to SQL

jhord, 2017-02-11:
A Web Form that asks for:

1.A Serial Number of the CATS hardware attached to the machine

2.The Machine type (FDM Printer, SLA , Laser etc..)
3. The Machine Name (Type A Series 1 Pro, Cube Pro etc..)

Closed 2017-02-11.

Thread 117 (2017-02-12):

Machine State Toggle Switch

jhord, 2017-02-12:
This switch will allow admins to control CATS remotely.

Resources:

http://www.bootstraptoggle.com/

jhord, 2017-02-12:
The Toggle Switch currently reads the database and displays the correct state of the switch.

The next step will be to create a query to $POST a flip of the switch to the database.

Sokhanetaze80, 2023-06-23:
12ib7dApVFvg82TXKycWBNpN8kFyiAN1dr

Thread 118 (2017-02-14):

CATS Weekly Blog Post

ophilli, 2017-02-14:
http://ci.clemson.edu/blogs/cats/wp-admin/

@jhord, @sabare3, you've got the first doubled up post of the semester. Due to the fact that you've got two people your post should be ~twice as long as a traditional post.

Please wait to publish yours until after @mbgroom.

Here are a few sample blog topics:

Hardware Team & Software Team Current Assignments & how they lead to the final goal
Personal Goals & Accomplishments for the Project
Technical Analysis of an aspect of the project
Please include lots of pictures!

Due 2017-02-20

ophilli, 2017-03-01:
@jhord @Sabare3 plz do the needful.

Closed 2017-03-10.

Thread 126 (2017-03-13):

CATS Enclosure Continuous Improvement

Sabare3, 2017-03-13:

Sabare3, 2017-03-16:
- Add slots on main faceplate holes for nut capture
- Fix through hole size for keypad by 1.8x (180%)

ophilli, 2017-04-07:
Stefan, please update.

Sabare3, 2017-04-11:
Updated

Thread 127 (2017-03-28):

Fix PCB LED

ophilli, 2017-03-28:
Shit's wack yo.

The footprint has been flipped across the centerline - meaning we need to mount our LEDs upside down.

Closed 2017-04-20.

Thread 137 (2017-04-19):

Unregistered Hostnames Result in Unhandled Exception

ophilli, 2017-04-19:
While testing Ace I realized that we are not handling the case where a node tries to look up it's host-name and receives no results back. This results in the Python code crashing.

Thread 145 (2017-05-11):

Set Temp Sensor I2C Address

ophilli, 2017-05-11:
Currently on the Pi HAT the temp sensor address pins are floating - this results in unreliable access to the sensor as we cannot know it's address on the bus.

ophilli, 2017-05-11:
[Adafruit Hardware Address Examples](https://learn.adafruit.com/adafruit-led-backpack/changing-i2c-address)
[Temp Sensor Datasheet](http://www.nxp.com/documents/data_sheet/LM75B.pdf)

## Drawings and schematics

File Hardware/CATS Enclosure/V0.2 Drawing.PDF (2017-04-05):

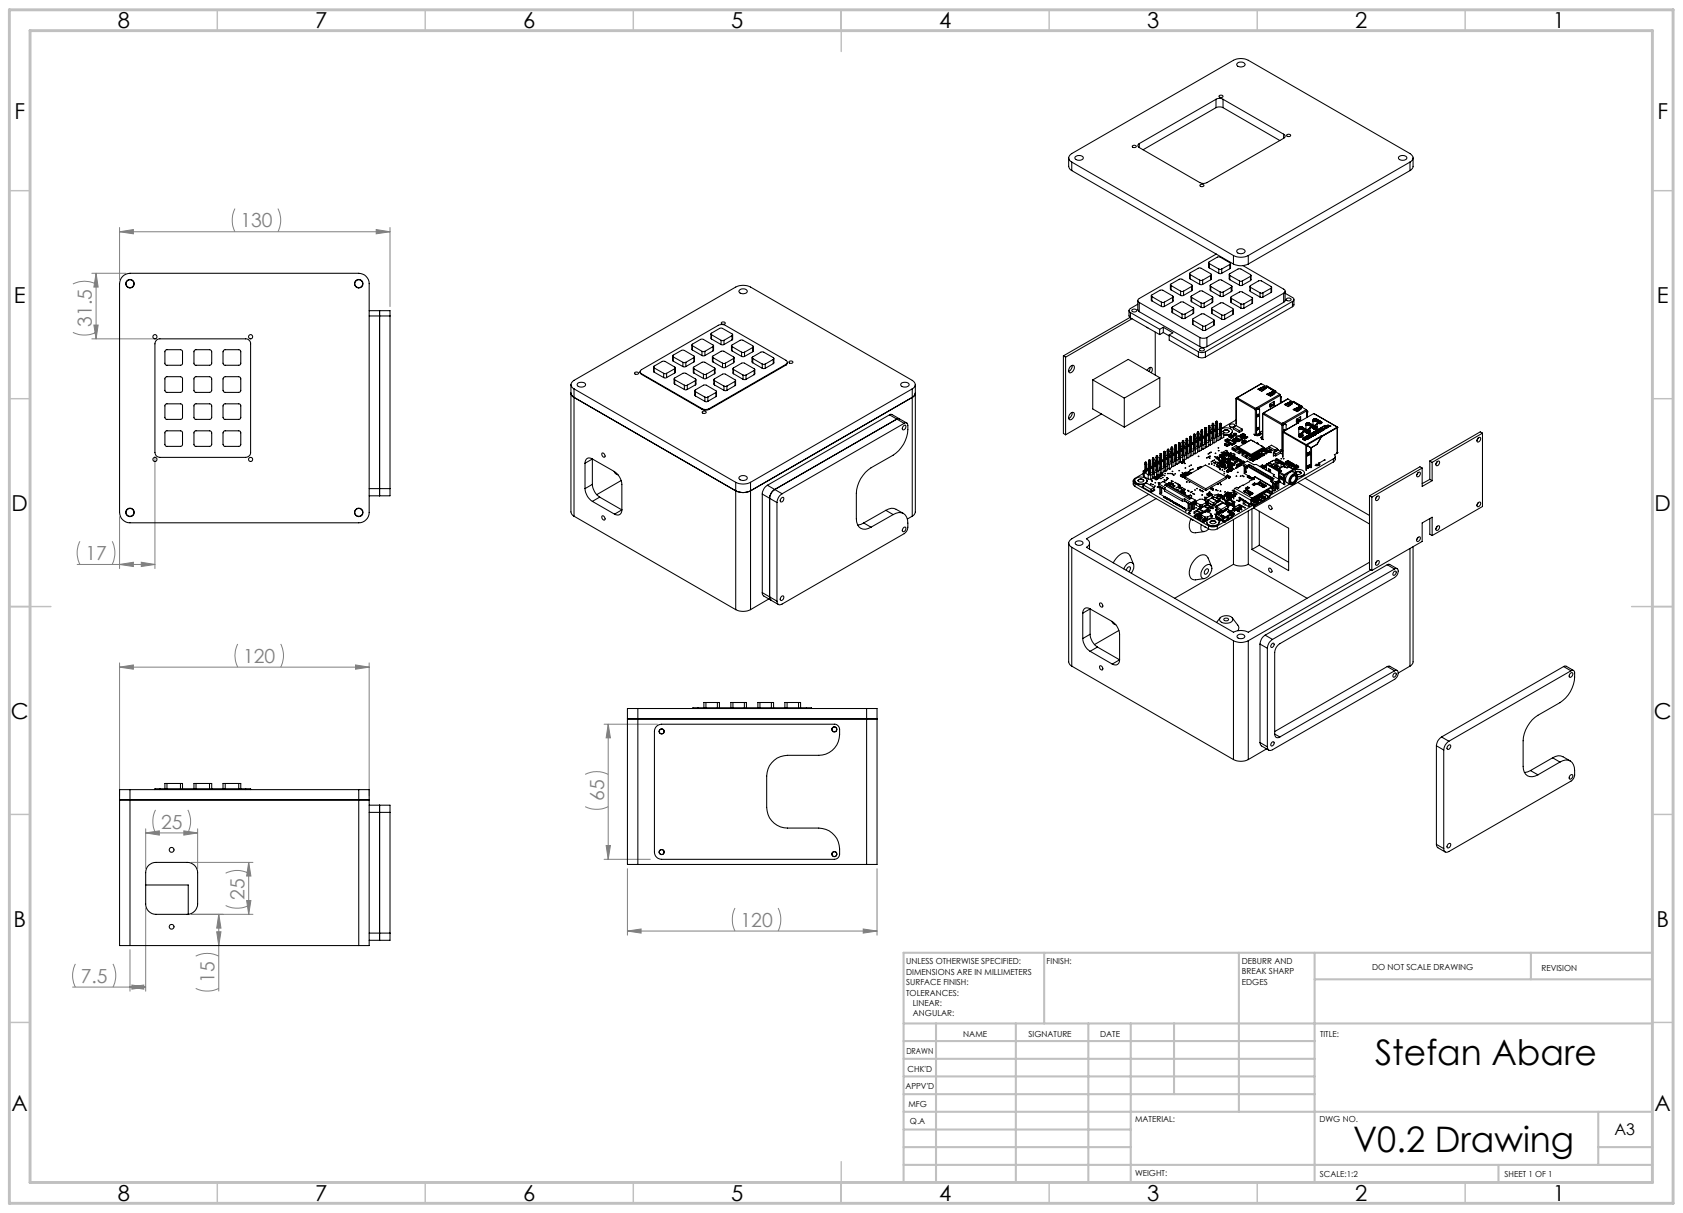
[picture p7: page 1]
FINISH:; DEBURR AND; BREAK SHARP; DO NOT SCALE DRAWING; REVISION; SCALE:1:2; SHEET 1 OF 1

UNLESS OTHERWISE SPECIFIED:
DIMENSIONS ARE IN MILLIMETERS
SURFACE FINISH:
TOLERANCES:
LINEAR:
ANGULAR:

NAME | SIGNATURE | DATE | | | | TITLE: Stefan Abare

DRAWN
CHK'D
APPV'D
MFG
Q.A | | | | MATERIAL: | DWG NO. V0.2 Drawing | A3

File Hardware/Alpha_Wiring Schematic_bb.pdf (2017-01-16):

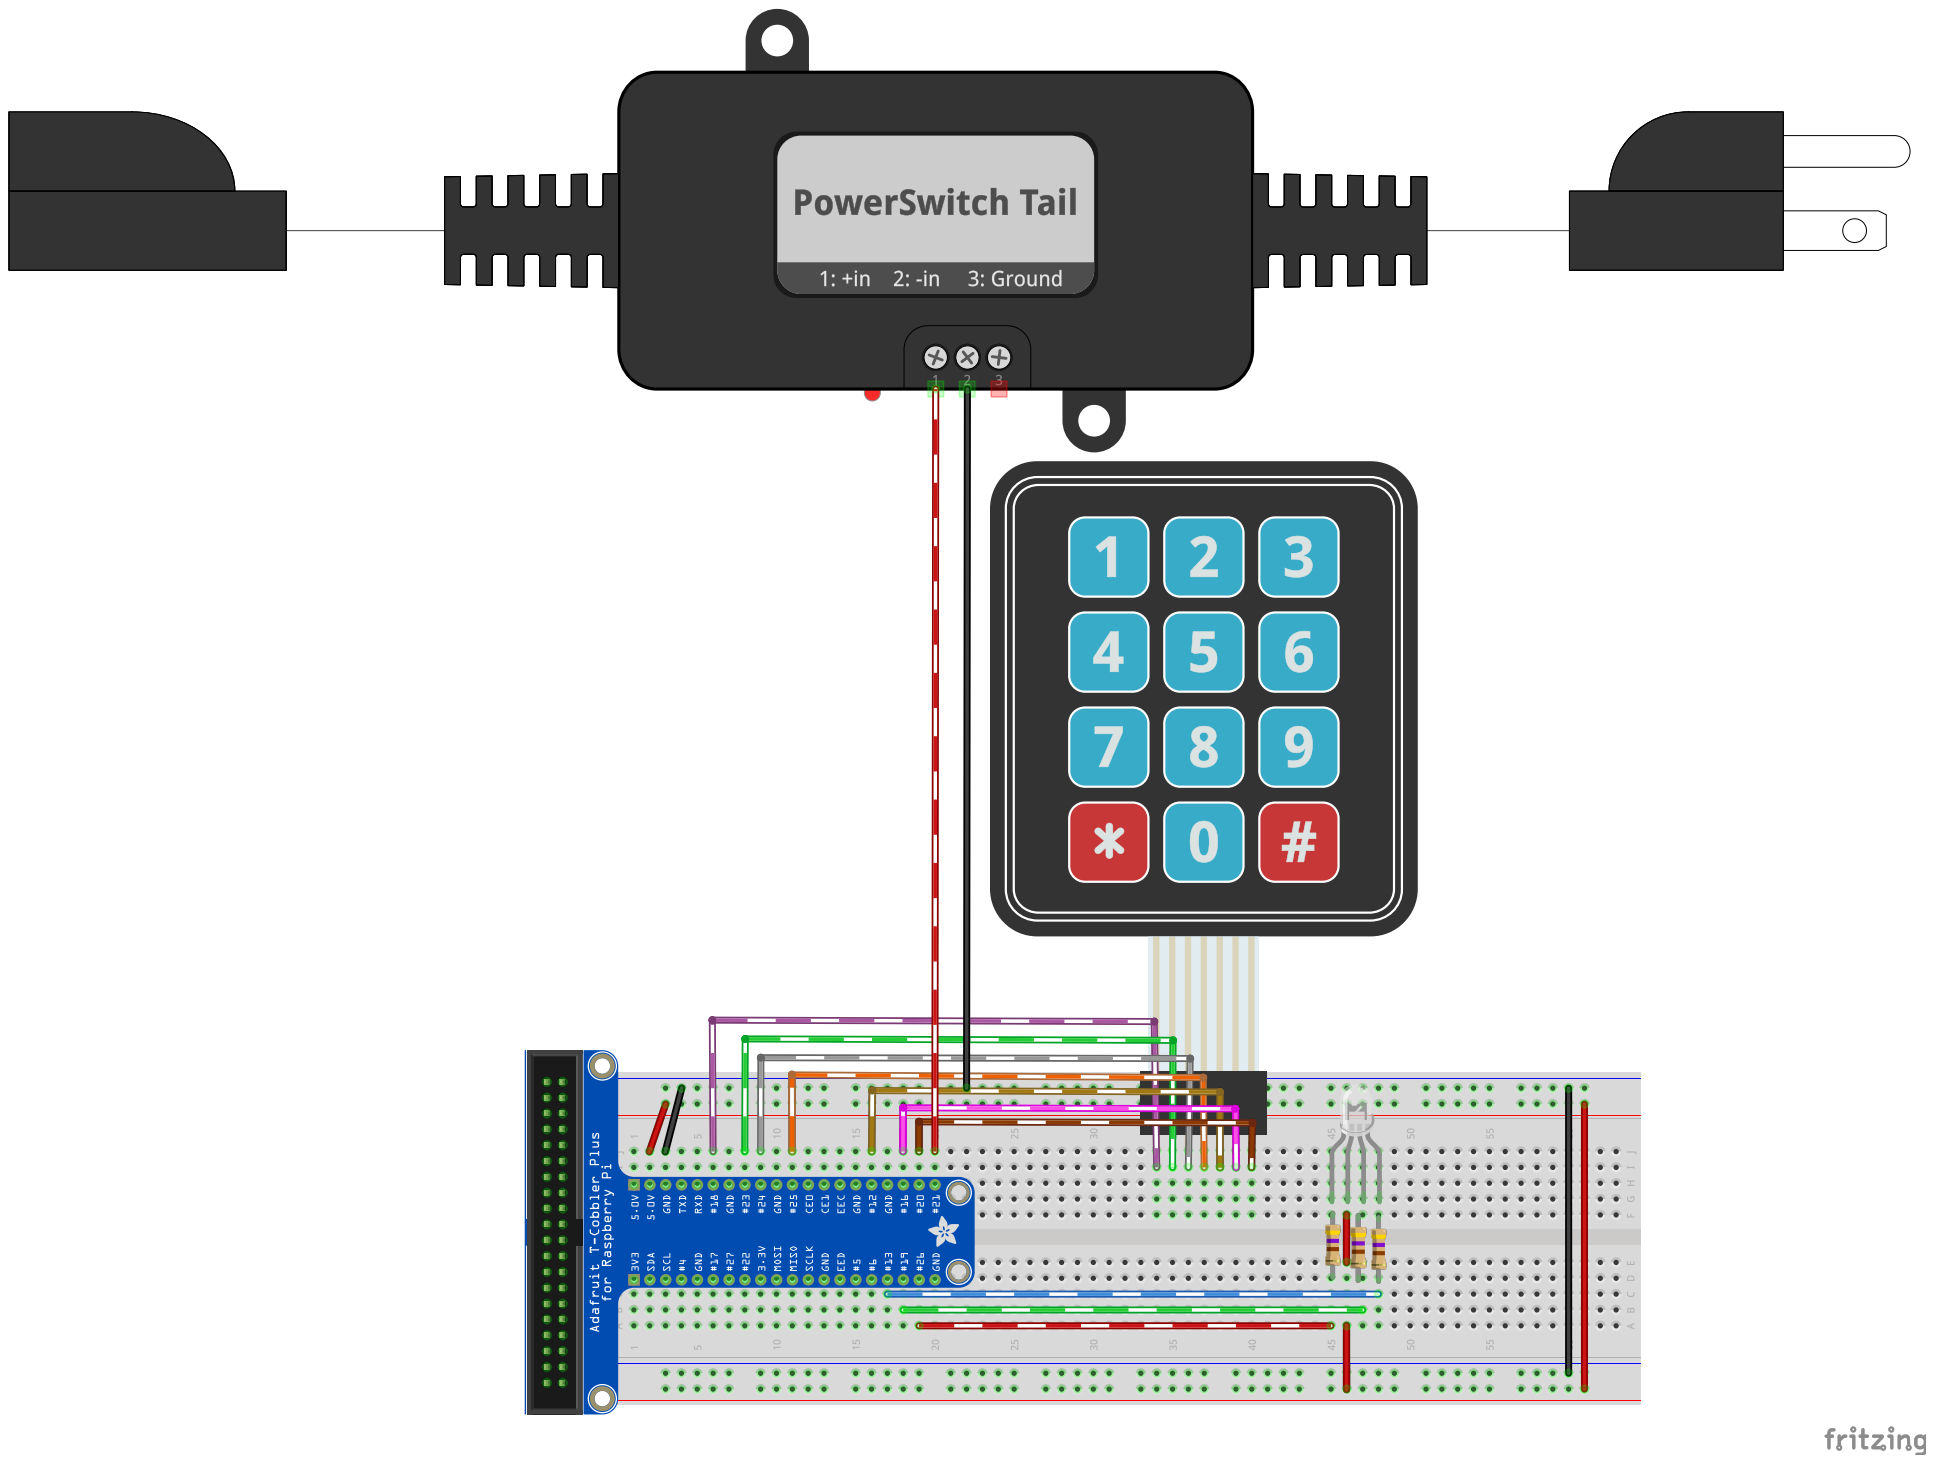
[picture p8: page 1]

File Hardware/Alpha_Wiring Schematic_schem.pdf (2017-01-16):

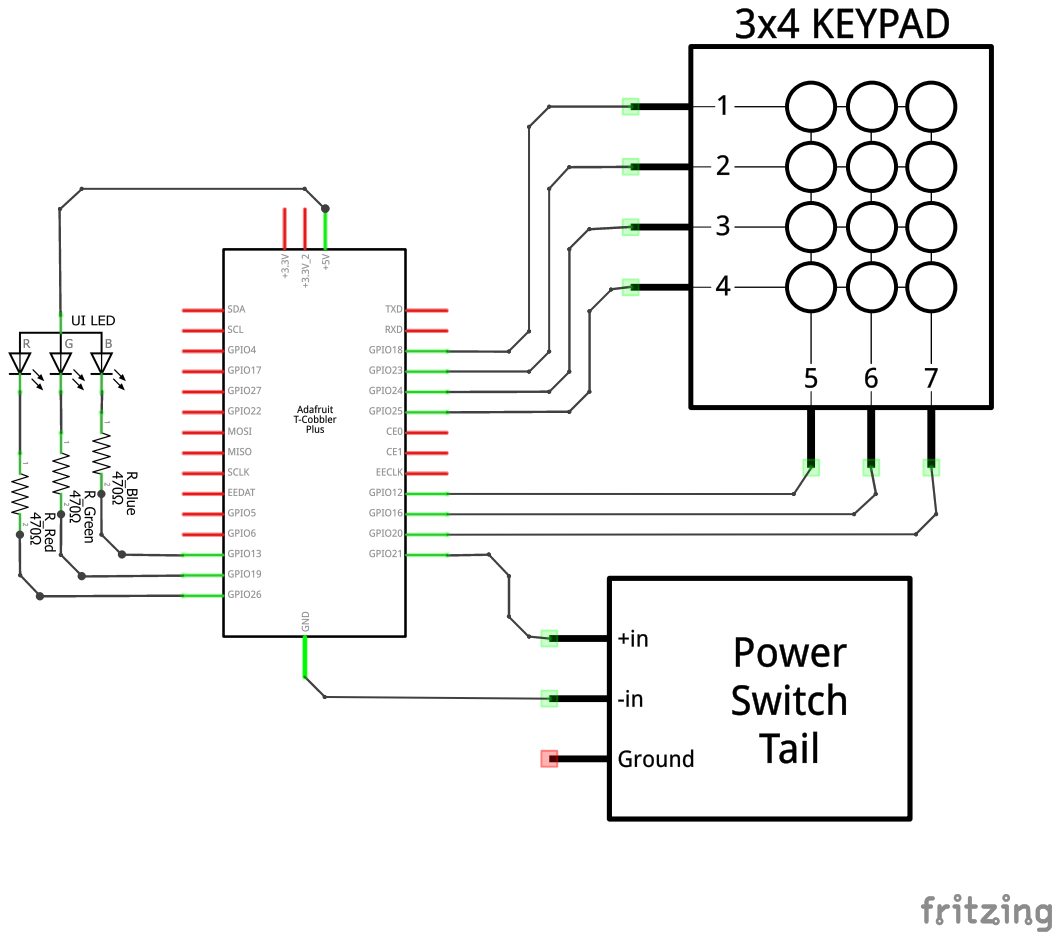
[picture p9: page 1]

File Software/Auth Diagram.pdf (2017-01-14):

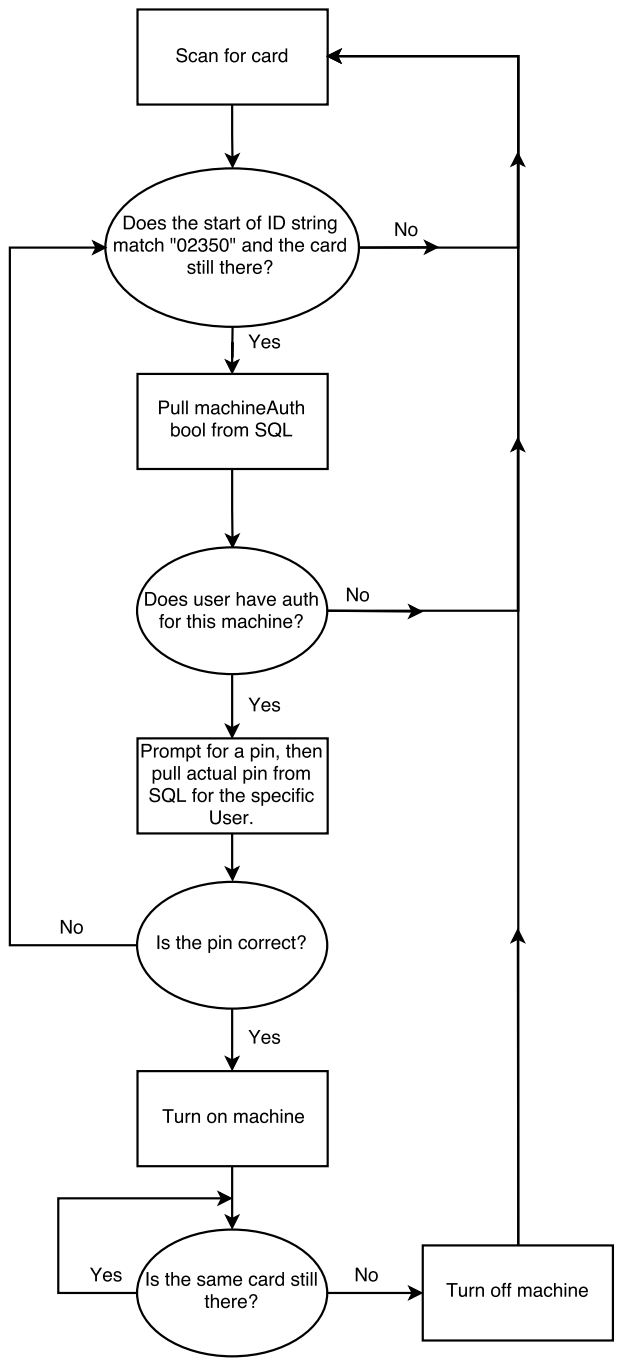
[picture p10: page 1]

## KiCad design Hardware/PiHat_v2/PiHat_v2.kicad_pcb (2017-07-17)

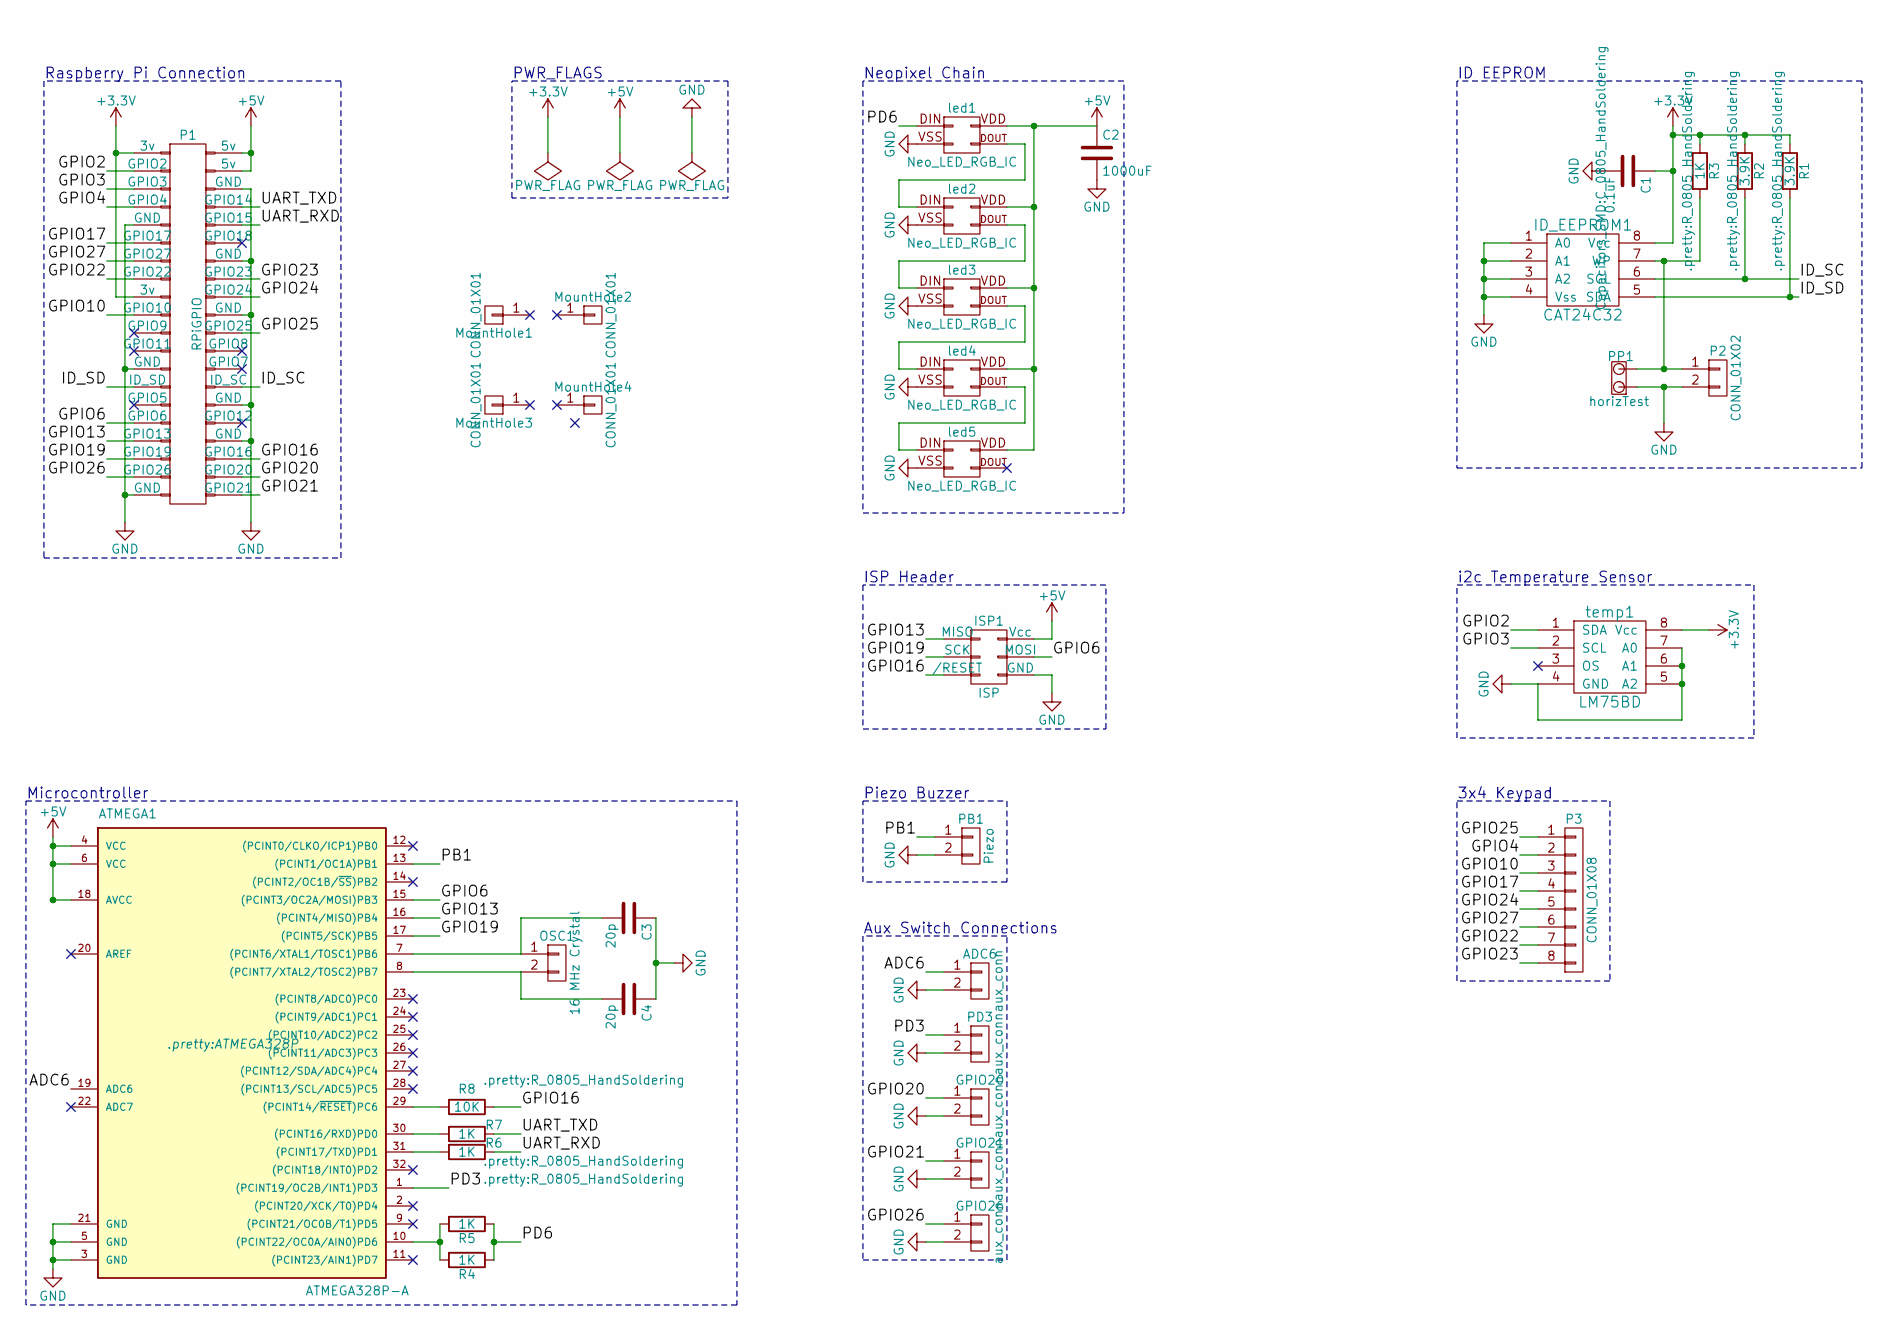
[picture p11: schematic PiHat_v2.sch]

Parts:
ADC6: aux_conn; Pin_Header_Straight_1x02_Pitch2.54mm
ATMEGA1: ATMEGA328P-A; ATMEGA328P
C1: 0.1uF; C_0805_HandSoldering
C2: 1000uF; AluCap_8mmDia_Nichicon
C3, C4: 20p; C_0603_HandSoldering
GPIO20, GPIO21, GPIO26: aux_conn; Pin_Header_Straight_1x02_Pitch2.54mm
ID_EEPROM1: CAT24C32; SOIC-8_3.9x4.9mm_Pitch1.27mm
ISP1: ISP; Pin_Header_Straight_2x03_Pitch2.54mm
MountHole1, MountHole2, MountHole3, MountHole4: CONN_01X01; raspiMountingHole
OSC1: 16 MHz Crystal; Crystal_SMD_HC49-SD
P1: RPiGPIO; Pin_Header_Straight_2x20_Pitch2.54mm
P2: CONN_01X02; Pin_Header_Straight_1x02_Pitch2.54mm
P3: CONN_01X08; Keypad_Ethernet
PB1: Piezo; Piezo_CT-1205h-smt
PD3: aux_conn; Pin_Header_Straight_1x02_Pitch2.54mm
PP1: horizTest; Test_Point_2Pads
R1, R2: 3.9K; R_0805_HandSoldering
R3, R6, R7: 1K; R_0805_HandSoldering; Tolerance 1%
R4, R5: 1K; R_0805_HandSoldering
R8: 10K; R_0805_HandSoldering; Tolerance 1%
led1, led2, led3, led4, led5: Neo_LED_RGB_IC; Neo_RGB_LED
temp1: LM75BD; SOIC-8_3.9x4.9mm_Pitch1.27mm

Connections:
+3V3: C1.1, ID_EEPROM1.8 (Vcc), P1.1 (3v), P1.17 (3v), R1.1, R2.1, R3.1, temp1.8 (Vcc)
+5V: ATMEGA1.4 (VCC), ATMEGA1.6 (VCC), ATMEGA1.18 (AVCC), C2.1, ISP1.2 (Vcc), P1.2 (5v), P1.4 (5v), led1.VDD, led2.VDD, led3.VDD, led4.VDD, led5.VDD
/ADC6: ADC6.1, ATMEGA1.19 (ADC6)
/GPIO2: P1.3 (GPIO2), temp1.1 (SDA)
/GPIO3: P1.5 (GPIO3), temp1.2 (SCL)
/GPIO4: P1.7 (GPIO4), P3.2
/GPIO6: ATMEGA1.15 ((PCINT3/OC2A/MOSI)PB3), ISP1.4 (MOSI), P1.31 (GPIO6)
/GPIO10: P1.19 (GPIO10), P3.3
/GPIO13: ATMEGA1.16 ((PCINT4/MISO)PB4), ISP1.1 (MISO), P1.33 (GPIO13)
/GPIO16: ISP1.5 (/RESET), P1.36 (GPIO16), R8.1
/GPIO17: P1.11 (GPIO17), P3.4
/GPIO19: ATMEGA1.17 ((PCINT5/SCK)PB5), ISP1.3 (SCK), P1.35 (GPIO19)
/GPIO20: GPIO20.1, P1.38 (GPIO20)
/GPIO21: GPIO21.1, P1.40 (GPIO21)
/GPIO22: P1.15 (GPIO22), P3.7
/GPIO23: P1.16 (GPIO23), P3.8
/GPIO24: P1.18 (GPIO24), P3.5
/GPIO25: P1.22 (GPIO25), P3.1
/GPIO26: GPIO26.1, P1.37 (GPIO26)
/GPIO27: P1.13 (GPIO27), P3.6
/ID_SC: ID_EEPROM1.6 (SCL), P1.28 (ID_SC), R2.2
/ID_SD: ID_EEPROM1.5 (SDA), P1.27 (ID_SD), R1.2
/PB1: ATMEGA1.13 ((PCINT1/OC1A)PB1), PB1.1
/PD3: ATMEGA1.1 ((PCINT19/OC2B/INT1)PD3), PD3.1
/PD6: R4.1, R5.1, led1.DIN
/UART_RXD: P1.10 (GPIO15), R6.1
/UART_TXD: P1.8 (GPIO14), R7.1
GND: ADC6.2, ATMEGA1.3 (GND), ATMEGA1.5 (GND), ATMEGA1.21 (GND), C1.2, C2.2, C3.1, C4.1, GPIO20.2, GPIO21.2, GPIO26.2, ID_EEPROM1.1 (A0), ID_EEPROM1.2 (A1), ID_EEPROM1.3 (A2), ID_EEPROM1.4 (Vss), ISP1.6 (GND), P1.6 (GND), P1.9 (GND), P1.14 (GND), P1.20 (GND), P1.25 (GND), P1.30 (GND), P1.34 (GND), P1.39 (GND), P2.2, PB1.2, PD3.2, PP1.1, led1.VSS, led2.VSS, led3.VSS, led4.VSS, led5.VSS, temp1.4 (GND), temp1.5 (A2), temp1.6 (A1), temp1.7 (A0); also elsewhere on the board
unnamed: ATMEGA1.7 ((PCINT6/XTAL1/TOSC1)PB6), C3.2, OSC1.1
unnamed: ATMEGA1.8 ((PCINT7/XTAL2/TOSC2)PB7), C4.2, OSC1.2
unnamed: ATMEGA1.10 ((PCINT22/OC0A/AIN0)PD6), R4.2, R5.2
unnamed: ATMEGA1.29 ((PCINT14/~RESET~)PC6), R8.2
unnamed: ATMEGA1.30 ((PCINT16/RXD)PD0), R7.2
unnamed: ATMEGA1.31 ((PCINT17/TXD)PD1), R6.2
unnamed 48: ID_EEPROM1.7 (WP), P2.1, PP1.2, R3.2; also elsewhere on the board
unnamed: led1.DOUT, led2.DIN
unnamed: led2.DOUT, led3.DIN
unnamed: led3.DOUT, led4.DIN
unnamed: led4.DOUT, led5.DIN

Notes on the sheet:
Raspberry Pi Connection
ID EEPROM
Neopixel Chain
3x4 Keypad
Aux Switch Connections
Piezo Buzzer
i2c Temperature Sensor
Microcontroller
ISP Header
PWR_FLAGS

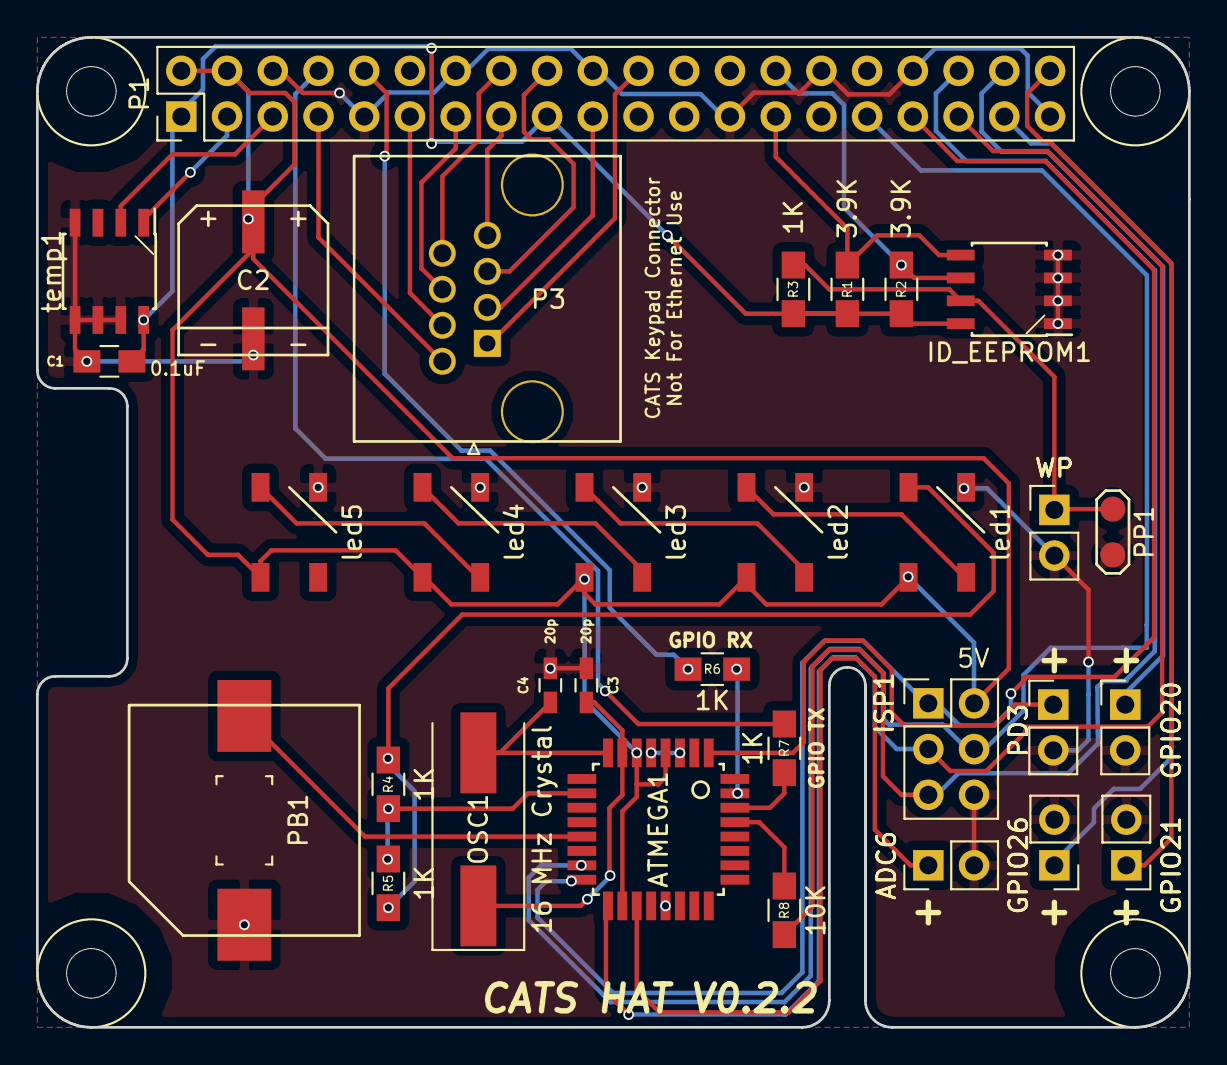
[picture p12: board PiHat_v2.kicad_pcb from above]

Board: 2 copper layers, 64.0 x 55.0 mm, 36 parts (0 on the bottom side), 39 nets.

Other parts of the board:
WP: CONN_01X02; Pin_Header_Straight_1x02_Pitch2.54mm

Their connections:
GND: WP.2; also elsewhere on the board
unnamed 48: WP.1; also elsewhere on the board

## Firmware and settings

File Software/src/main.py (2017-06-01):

#########################################################################
#    USAGE: python3 main.py                                             #
#                                                                       #
#    MAKE SURE YOU USE PYTHON3 OTHERWISE YOU'RE GOING TO GET ERRORS!	#
#                                                                       #
#########################################################################

from keypad import *
from on_off import *
from rpiCardScan import *
import sql
import time
import signal
import sys
import pymysql
import datetime
import os

if __name__ == '__main__':
    # initialize the keypad and important variables
    kp = keypad()
    ID = None; readpad = 0; join = 0; character = 0; length = 0;
    pinArray = [];
    db = sql.SQL()

    # While the same card is still being read then do the following:
    # ask for PIN and search the SQL database to find the user
    while True:
        count = 0
        flag = False
        check_opt = False
        # Ask for input from the RPI, if no input within __ seconds then quit
        ID = RPICardScan()
        holdID = ID
        while (ID == holdID and holdID != None and holdID[0:5] == "02350"):
            try:
                author = db.setMachAuth(ID)
                # USER IS NOT AUTHORIZED SO PUT IN ID AGAIN
                if (author == True):
                    break

                # Loop that prompts if the PIN was incorrect then re-enter it
                while (flag == False):
                    #blinkKey2()

                    # Get User Optional PIN
                    opt = db.getUser2FA(holdID)
                    # Get Machine Optional PIN
                    mopt = db.getMachineOPT()
                    # Check if the user needs to put in PIN or not
                    check_opt = db.check2FA(opt, mopt) # should ignore mopt

                    # Passes through if user does not need PIN
                    # Otherwise, ask the user for a PIN
                    if (check_opt == True):
                        flag = True
                        break
                    else:
                        pinArray = None
                        # if the user has attempted their PIN 3 times then quit
                        if (count == 3):
                            CUID = db.getCUID(holdID)
                            db.eventLog(CUID, 4)
                            break

                        count = count + 1

                        # interrupt handler that sets a timer in the background
                        signal.signal(signal.SIGALRM, kp.timer)
                        signal.alarm(7)

                        try:
                            # type in the user's PIN
                            pinArray = kp.KeyPadAuthor()

                            # function to check if user exists and if PIN is correct
                            flag = db.twoFactorAuth(ID, pinArray)

                        except:
                            break
                # disable the interrupt handler timer
                signal.alarm(0)

                holdID = RPICardScan()
                # if PIN is incorrect and card is still there: ask to re-enter PIN
                if flag == False and holdID != None:
                    continue
                # if card has been taken off after timer: re-prompt to scan card
                elif holdID == None:
                    break
                # Otherwise this means PIN is good and user is still there. Give access
                else:
                    pass

                pinArray = []
                while (holdID != None and holdID[0:5]!="02350"):
                    holdID = RPICardScan()


            except KeyboardInterrupt:
                print ("")
                TurnPowerOff()
                sys.exit(0)
        # turn off the power if it's been turned on
        TurnPowerOff()

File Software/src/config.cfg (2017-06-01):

[_sql]
	hostname =
	database =
	username =
	password =

[_led]
	count 			= 1
	pin 				= 18
	freq_hz 		= 800000
	dma 				= 5
	brightness 	= 255
	invert 			= false

[_relay]
	pin = 4

[_buzzer]
	pin = 17

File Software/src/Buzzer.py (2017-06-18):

# http://www.linuxcircle.com/2015/04/12/how-to-play-piezo-buzzer-tunes-on-raspberry-pi-gpio-with-pwm/
# Dipto Pratyaksa

import RPi.GPIO as GPIO   #import the GPIO library
import time               #import the time library

import os
import configparser

config = configparser.RawConfigParser() #instantiate config reader
config.read(os.path.join(os.path.abspath(os.path.dirname(__file__)), 'config.cfg')) #actually read the config file

class Buzzer(object):
 def __init__(self):
  GPIO.setmode(GPIO.BCM)
  self.buzzer_pin = int(config.get('_buzzer', 'pin')) #set to GPIO pin 17 for CATS HAT
  GPIO.setwarnings(False)
  GPIO.setup(self.buzzer_pin, GPIO.IN)
  GPIO.setup(self.buzzer_pin, GPIO.OUT)
  print("buzzer ready")

 def __del__(self):
  class_name = self.__class__.__name__
  print (class_name, "finished")

 def buzz(self,pitch, duration):   #create the function “buzz” and feed it the pitch and duration)

  if(pitch==0):
   time.sleep(duration)
   return
  period = 1.0 / pitch     #in physics, the period (sec/cyc) is the inverse of the frequency (cyc/sec)
  delay = period / 2     #calcuate the time for half of the wave
  cycles = int(duration * pitch)   #the number of waves to produce is the duration times the frequency

  for i in range(cycles):    #start a loop from 0 to the variable “cycles” calculated above
   GPIO.output(self.buzzer_pin, True)   #set pin 18 to high
   time.sleep(delay)    #wait with pin 18 high
   GPIO.output(self.buzzer_pin, False)    #set pin 18 to low
   time.sleep(delay)    #wait with pin 18 low

 def play(self, tune):
  GPIO.setmode(GPIO.BCM)
  GPIO.setup(self.buzzer_pin, GPIO.OUT)
  x=0

  print("Playing tune ",tune)
  if(tune==1):
    pitches=[262,294,330,349,392,440,494,523, 587, 659,698,784,880,988,1047]
    duration=0.1
    for p in pitches:
      self.buzz(p, duration)  #feed the pitch and duration to the function, “buzz”
      time.sleep(duration *0.5)
    for p in reversed(pitches):
      self.buzz(p, duration)
      time.sleep(duration *0.5)

  elif(tune==2):
    pitches=[262,330,392,523,1047]
    duration=[0.2,0.2,0.2,0.2,0.2,0,5]
    for p in pitches:
      self.buzz(p, duration[x])  #feed the pitch and duration to the function, “buzz”
      time.sleep(duration[x] *0.5)
      x+=1
  elif(tune==3):
    pitches=[392,294,0,392,294,0,392,0,392,392,392,0,1047,262]
    duration=[0.2,0.2,0.2,0.2,0.2,0.2,0.1,0.1,0.1,0.1,0.1,0.1,0.8,0.4]
    for p in pitches:
      self.buzz(p, duration[x])  #feed the pitch and duration to the func$
      time.sleep(duration[x] *0.5)
      x+=1

  elif(tune==4):
    pitches=[1047, 988,659]
    duration=[0.1,0.1,0.2]
    for p in pitches:
      self.buzz(p, duration[x])  #feed the pitch and duration to the func$
      time.sleep(duration[x] *0.5)
      x+=1

  elif(tune==5):
    pitches=[1047, 988,523]
    duration=[0.1,0.1,0.2]
    for p in pitches:
      self.buzz(p, duration[x])  #feed the pitch and duration to the func$
      time.sleep(duration[x] *0.5)
      x+=1

  GPIO.setup(self.buzzer_pin, GPIO.IN)

if __name__ == "__main__":
  a = input("Enter Tune number 1-5:")
  buzzer = Buzzer()
  buzzer.play(int(a))

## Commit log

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2016-11-11 Update to main.py
    fixed some warnings for sql command
    [main.py]
2016-11-12 Update on_off.py
    fixed code, added more comments.
    [on_off.py]
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2016-11-12 Correct EOL ^M on Linux
    [keypad.py]
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2016-11-14 temporary fix to user not authorized errors
    [main.py]
2016-11-18 V16-11.2 to Master (#50)
    * deleted rpi command that makes error
    * trying to print & type 4 keys without exiting
    * Working keyboard matrix
    * removed folder
    * added matrix folder and working code
    * Create scanCard.py
    * added working on/off power switch code
    * Update README.md
    * don't need the folder, just the code
    * un-needed files already in te master
    * Create README.md
    * On and Off PowerSwitch Tail Control
    * added working authentication code
    * Update rpiCardScan.py
    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
    [keypad.py, main.py, on_off.py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]
2016-12-13 Completed Enhancements (#53)
    G committed some sensitive information here. Hopefully these can be deleted.
    * Add files via upload
    * updated working ISAM prototype
    * update prototype
    * temp fix to user not authorized error
    * Create ISAM Poster
    * ISAM Poster
    * Delete ISAM Poster
    * LED blink, SQL Error Log, Admin Email are added
    * Update main.py
    * Update main.py
    * Update keypad.py
    * Update on_off.py
    * Update ErrorSQL.py
    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
    [keypad.py, main.py, on_off.py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]
2017-01-13 Correct Auth Details for Demo
    [main.py]
2017-01-13 Update main.py (#59)
    This will be necessary until we resolve #60.
    [main.py]
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2017-01-15 Fix to Issue #68
    Fixed blinkKey() in keypad.py and on_off.py. There might be another file
    but I fixed the specific things asked for.
    [keypad.py, on_off.py]
2017-01-16 commit hardware designs into devel (#72)
    Added hardware files to the repository.
    Uploaded files for pihat
    Fritzing breadboard layout files
    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
    [Alpha_Wiring Schematic.fzz, CATSiges.iges, CATSobj.obj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]
2017-01-17 More funky indent correction
    [main.py, rpiCardScan.py]
2017-01-20 Fixed the Invalid PIN re-prompt bug
    [keypad.py, main.py, on_off.py]
2017-01-20 reset timer after key pressed
    [keypad.py]
2017-01-22 Error logging # 4 added and tally of PIN attempt
    [main.py]
2017-01-25 PiHat_v2 - A New Hope
    Hoping to cut out a lot of the bullshit from the PiHAT designs. I've
    designed the edge cuts from the specifications listed in the [HAT board
    specification.](https://github.com/raspberrypi/hats/blob/master/hat-board-mechanical.pdf)
    [PiHat_v2.kicad_pcb, PiHat_v2.sch]
2017-01-25 Implement EEPROM and RPI GPIO Connection Schematics
    I've added the EEPROM circuit and the RPIO GPIO to the schematics, as
    well as associated the proper footprints with them.
    [idEEPROM.sch, rpiGPIO.sch]
2017-01-25 Correct EEPROM Schematic - Add Pin Numbers
    [PiHat_v2.kicad_pcb, PiHat_v2.sch]
2017-01-25 Rough Sketch of Schematic and all Footprints Complete
    * I've completed a first draft of the schematic, and verified that all
    parts have a footprint.
    * Next steps include routing the PCB, verifying the designs, and
    including any changes.
    [PiHat_v2.kicad_pcb, PiHat_v2.sch]
2017-01-25 Complete First Draft of Routing
    [PiHat_v2.kicad_pcb]
2017-01-25 Complete Ground Plane and Keepout Zones
    [PiHat_v2.kicad_pcb]
2017-01-25 Implement Mounting Holes & Remove Improper Keepout Areas
    This board should be electrically sound - and looks to me like it has
    all the right parts at first glance. There are some definite silk-screen
    improvements that can be made, however.
    [PiHat_v2.kicad_pcb]
2017-01-25 One final thing . . .
    Sorry Stefan.
    [CATSiges.iges, CATSobj.obj, CATSstl.stl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]
2017-01-31 Added brief config file
    Will be implementing it into the actual code now.
    [config.cfg]
2017-01-31 Update config.cfg
    Added new line, mind explaining why the new line is necessary?
    [config.cfg]
2017-02-01 Insert Missing Via
    I was missing a via in the lower right of the board - it has now been
    re-inserted.
    [PiHat_v2.kicad_pcb]
2017-02-03 New Schematic for PiHat
    [PiHat_v2.sch]
2017-02-16 Finished PiHat v2 Design
    [PiHat_v2.kicad_pcb, PiHat_v2.sch]
2017-02-20 Finished PiHat v2 Design (#120)
    Added a period to the end of the sentence
    * New Schematic for PiHat
    * Finished PiHat v2 Design
    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
    [PiHat_v2.kicad_pcb, PiHat_v2.sch]
2017-03-01 SQL Fix Closes #104 (#121)
    * Update requirements.txt
    * Update 0.1?
    Not really sure
    * Update AuthenticationSQL.py
    * Update AuthenticationSQL.py
    Okay so I fixed how we get the stuffs from the SQL. There were a few things that were pretty screwy. So now we look up "authType" using "PiHostname" in the SQL, then look up the variable that authType is for ID in user. This is what is returned in machineAuth. For some reason, we had machineAuth returning the current machine, which makes no sense as we try to use it as a boolean later in the program but also as a machinetype in the SQL call in line 54, 55. This is like really stupid and needs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
    [main.py]
2017-03-29 Neopixel Footprint Fix
    Rearranged the neopixel terminals to correctly mount it. Moved around
    silk screen references and changed the text to better understand the
    design when soldering. Added the developers' names to the back of the
    board.
    [PiHat_v2.kicad_pcb]
2017-04-05 PiHat Completion
    References for footprints are placed and named more efficiently. The pi
    header footprint is now on the back of the board and all connections to
    it were corrected. Added "+"s to the AUX references to show which side
    is positive and those reference texts are now what GPIO pin connects to
    it. Some footprints that are for components that are polarized or need
    to be placed a certain way were redone to show the orientation of the
    component for more efficient placement.
    [PiHat_v2.kicad_pcb]
2017-04-05 Added CATS Enclosure Files for SolidWorks (#125)
    * Added CATS Enclosure Files for SolidWorks
    CATS Enclosure V0.2
    * Dimensioned Drawings
    Dimensioned Drawings of the V0.2 enclosure + Exploded view.
    [V0.2 Drawing.SLDDRW]
2017-04-05 Revert "PiHat Completion"
    This reverts commit 6738365f23747a299ba35bc740daefcfdec640b0.
    [PiHat_v2.kicad_pcb]
2017-04-05 Revert "Revert "PiHat Completion""
    This reverts commit 9dfad16c77172f9cc3f0b0126633a712500f49b7.
    [PiHat_v2.kicad_pcb]
2017-04-11 Fixed piHat (#128)
    * Neopixel Footprint Fix
    * PiHat Completion
    is positive and those reference texts are now what GPIO pin conne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
    [PiHat_v2.kicad_pcb]
2017-04-11 New piHat
    [PiHat_v2.kicad_pcb]
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2017-04-13 Thor's Base PCB Design
    This is the design that Thor attempted to commit to github in PR #130.
    It consists of the 'Finished PiHAT v2 Design', the 'Neopixel Footprint
    Fix', and the addition of our names on the silkscreen.
    [PiHat_v2.kicad_pcb]
2017-04-18 Make the PCB Pretty Again (#134)
    * Implement OSHW Copper Logo on PiHAT
    * Implement CI, Makerspace, Paw Logo on PiHAT
    * Archive final PiHAT_v0.2.1 Design
    This is a simple .zip archive of the final PiHAT_v0.2.1 design.
    * Redraw Fill Zones on PiHAT v0.2.1
    Whoops - Forgot to redraw the fill zones. That's been remedied!
    [PiHat_v2.kicad_pcb]
2017-04-26 why is G writing commits to my repo? Fixes Neopixel Support Commit after #138 (#139)
    * Simple Bash Script to test SSH Tunnel for SQL Nodes
    * SQL Statements have been modified to fit the new SQL Database
    * SQL Statements have been modified and GPIO pins
    * Preliminary NeoPixel Support
    Accessing the Neopixels is tough.
    - This file has to be run as root due to the direct memory access.
    - Colors are listed as GBR despite documentation stating otherwise
    - Several global variables are used in this module - should not be like tihs
    - Synchronizing the beeping and LEDs still needs to be done
    - This needs to be tested within the CATS ecosystem
    [on_off.py]
2017-04-26 migrate from scan_key to src
    [config.cfg]
2017-04-26 Getting Ready For Maker Day (#140)
    * starting to implement optional two-factor authentication
    * starting to implement optional two-factor authentication
    * Adding audio files
    * Added Audio effect to successful & unsuccessful login
    * added the main components that I know of
    * deleted function (will implement later if needed) and removed pygame from requirements.txt and header
    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
    [config.cfg]
2017-04-27 Fixed toggle button CSS for Brad
2017-06-01 SQL Refactoring & Closes #141 (#147)
    * Update configparser version
    * Add nose to requirements.txt
    * Travis-CI Support
    * Correct Nose Command
    * Update Commenting in rpiCardScan
    * LED & Relay Info in Config
    * Update Buzzer.py to use Config File for pin
    * Refactor on_off.py
    * Update Imports for led and buzzer
    * Import os for ConfigParser calls
    * Update Indentation in Main
    * Refactor SQL Code
    * Rudimentary Testing
    * Correct _led config.cfg
    [config.cfg]
2017-06-14 New PCB With ATMEGA Chip (#148)
    is positive and those reference texts are now what G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
    [PiHat_v2.kicad_pcb, PiHat_v2.sch]
2017-06-14 Fixes #148 (#149)
    is positive and those reference texts are now what GPIO pin connec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
    [PiHat_v2.kicad_pcb, PiHat_v2.sch]
2017-06-16 Merge remote-tracking branch 'refs/remotes/clemsonMakerspace/devel' into devel
    # Conflicts:
    # Hardware/PiHat_v2/.pretty/Neo_RGB_LED.kicad_mod
    # Hardware/PiHat_v2/PiHat_v2.kicad_pcb
    # Hardware/PiHat_v2/PiHat_v2.kicad_pcb-bak
    # Hardware/PiHat_v2/PiHat_v2.net
    # Hardware/PiHat_v2/PiHat_v2.pro
    [PiHat_v2.sch, config.cfg]
2017-06-16 Fixes Thor's Misery (#151)
    is positive and those reference texts are now what GPIO p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
    [PiHat_v2.kicad_pcb]
2017-06-16 Fixed my branch and moved ethernet port
    [PiHat_v2.kicad_pcb, PiHat_v2.sch]
2017-06-17 Schematic for Neopixel Chain & ISP Program Header
    I've chained 5 Neopixels and added an ISP header for the ATMEGA.
    [PiHat_v2.sch]
2017-06-17 Add PWR_FLAG to Schematic
    Solves "Pin connected to some other pins but no pin to drive it ERC
    error.
    [PiHat_v2.sch]
2017-06-17 Update Aux Connector Pin Directions
    [PiHat_v2.sch]
2017-06-17 Take AREF off 5v for ATMEGA
    [PiHat_v2.sch]
2017-06-17 Adjust Schematic Styling
    [PiHat_v2.sch]
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2017-06-17 Correct RPiGPIO and Crystal Footprints
    [PiHat_v2.sch]
2017-06-17 Move to SMT Piezo Buzzer
    [PiHat_v2.sch]
2017-06-17 Implement Mounting Holes in Schematic for Netlist Use
    [PiHat_v2.sch]
2017-06-17 Replace Mounting Holes and RPiGPIO Header
    [PiHat_v2.kicad_pcb]
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2017-06-17 Route all traces on PCB
    [PiHat_v2.kicad_pcb, PiHat_v2.sch, _saved_PiHat_v2.sch]
2017-06-17 Adjust silkscreen layer in footprints to display pin #s
    [PiHat_v2.kicad_pcb, PiHat_v2.sch]
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2017-06-17 Tweak Silkscreen of Resistors and Capacitors
    [PiHat_v2.kicad_pcb]
2017-06-17 Silkscreen Finalized Pending Review
    [PiHat_v2.kicad_pcb]
2017-06-17 Adjust Silkscreen Layout on PCB
    [PiHat_v2.kicad_pcb]
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2017-06-19 Implement AluCap in PCB
    [PiHat_v2.sch]
2017-06-19 Connect New Keypad GPIO Schema
    [PiHat_v2.kicad_pcb]
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2017-06-19 YASA - Yet Another Silkscreen Adjustment
    [PiHat_v2.kicad_pcb]
2017-06-19 Update Version Number of PiHat
    [PiHat_v2.kicad_pcb]
2017-06-19 Rotate AluCap for Proper Polarity
    [PiHat_v2.kicad_pcb, PiHat_v2.sch]
2017-06-19 Fix BOM Whitespace
2017-06-19 Pi Hat - now with non-imaginary components (#155)
    * Adjust Silkscreen Layout on PCB
    * Add 1000uF AluCap Footprint & Rename 100nF to 0.1uF
    * Implement AluCap in PCB
    * Connect New Keypad GPIO Schema
    * Built the BOM
    * Move Silkscreen Logo
    * YASA - Yet Another Silkscreen Adjustment
    * Update Version Number of PiHat
    * Rotate AluCap for Proper Polarity
    * Fix BOM Whitespace
    [PiHat_v2.kicad_pcb, PiHat_v2.sch]
2017-06-28 New ATMEGA Code
    Code controls neopixel and piezo buzzer from ATMEGA chip on new Pi-Hat
    [atmega_demo.ino]
2017-06-28 Connect GPIO RX and ATMega TX - Enlarge select silkscreen graphics
    [PiHat_v2.kicad_pcb, PiHat_v2.sch]
